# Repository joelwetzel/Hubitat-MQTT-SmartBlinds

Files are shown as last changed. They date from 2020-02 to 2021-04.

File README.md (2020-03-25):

# Hubitat MQTT SmartBlinds
**Hardware, Firmware, and Hubitat Driver for MQTT Smart Blinds**

This is a work in progress.  I don't expect anyone else will ever build one of these, but I wanted to document it, for my own ease of replicating it again.

The hardware and firmware is heavily based on the work of Smart Home Hookup here:  https://github.com/thehookup/Motorized_MQTT_Blinds, and here:  http://www.thesmarthomehookup.com/automated-motorized-window-blinds-horizontal-blinds/  Much thanks to that dude!  Watch his youtube video before following my instructions.

The Hubitat driver is my own creation, using the MQTT support that Hubitat added last year.

What I've tried to do that is beyond what Smart Home Hookup did is two things:
- Make it work well with Hubitat
- "Productize" it.  Hide all the hardware details and make it clean and minimal, repeatable to build, and easy to maintain.

----------

## Parts List
Stepper Motors: https://amzn.to/2D5rVsF

Stepper Drivers: https://amzn.to/2OZqW1W

NodeMCU: https://amzn.to/2I89xDF

Buck Converter: https://amzn.to/2UsQ7jA

12V Power Supply: https://www.amazon.com/gp/product/B07THWH1KZ

DC extension cables and barrel connector:  https://www.amazon.com/gp/product/B01EAHRZEC

Cheap ethernet cable to cut up:  https://www.amazon.com/gp/product/B074NBWQST

Ethernet coupler:  https://www.amazon.com/gp/product/B01CLFCX7E

Velcro strips:  https://www.amazon.com/Command-Picture-Decorate-Damage-Free-PH206-14NA/dp/B073XR4X72

Dupont Crimper toolset:  https://www.amazon.com/gp/product/B07GS1Z3M3

----------

## Preparing the Motor Assembly

#### The motor assembly goes into the blinds header.  It has a 3d printed base, the stepper motor itself, a 3d printed adapter to connect the motor to the rod, the driver board, and an ethernet cable sticking out.

1. Print the 2" blinds base:  https://github.com/thehookup/Motorized_MQTT_Blinds/blob/master/BlindsBase.stl.  It can be 30% infill.  Test-fit the stepper in it.  It should fit snugly.  You won't need screws or glue to hold it in, when in place in the blinds.

2. Open the blue cover on the stepper motor and use a screwdriver to scratch out the middle trace.  Use a multimeter to make sure continuity is broken.

3. Shorten the motor wires.  You can completely remove the middle one that went to the middle trace.  Shorten the others to 2.5 inches.  Attach a 4-pin female Dupont connector as shown.  I found this video very helpful for learning how to use my Dupont crimper:  https://www.youtube.com/watch?v=-u1t7Cdf6RE&t=376s

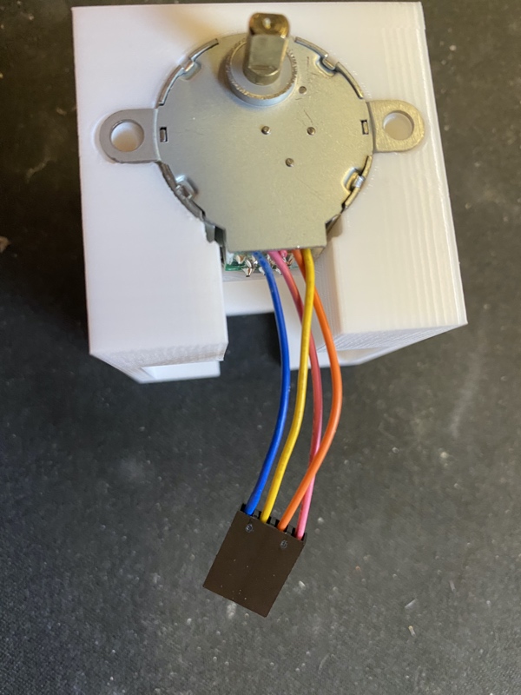
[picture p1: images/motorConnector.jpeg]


4. Prepare the stepper driver board.  You need to create a solder bridge between the reset pin and the sleep pin (the green jumper in this pic), and trim off any unused pins.

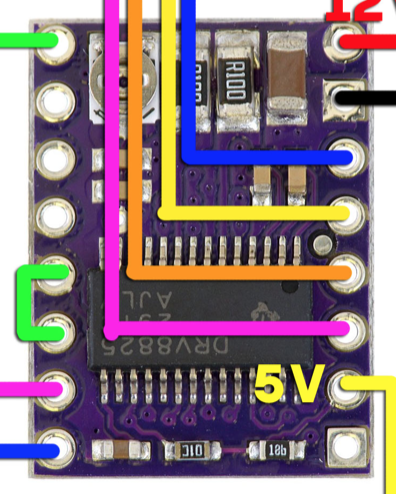
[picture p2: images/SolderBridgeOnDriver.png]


5. Pull down your blinds.
6. Remove any end caps, if it has them.
7. Remove the pull string assembly that turns the rod when you pull the strings.

8. You'll need to print an adapter to connect the stepper shaft to the rod in the blinds.  The rods can have lots of different shapes.  Smart Home Hookup provided several options.  I designed my own, since my rod had a profile like the superman emblem.  I've uploaded that STL here. (Adapter.stl)  Print it at 100% infill.  (By this point, you should have your blinds partially dismantled.  Smart Home Hookup has a good youtube video on doing that.)

9. Prepare the ethernet cable that will come out of the motor assembly.  It should be about 6 inches long.  Attach Dupont connectors as shown here:

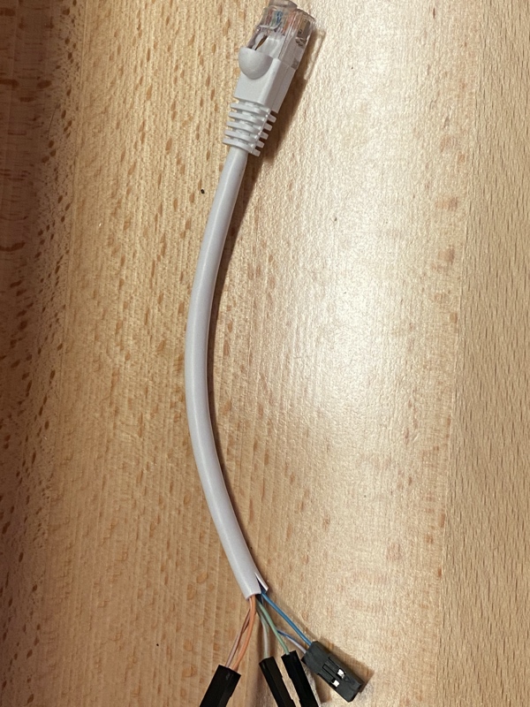
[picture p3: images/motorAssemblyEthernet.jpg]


10. Attach the connectors from both the ethernet cable and the motor onto the driver board, as shown here:

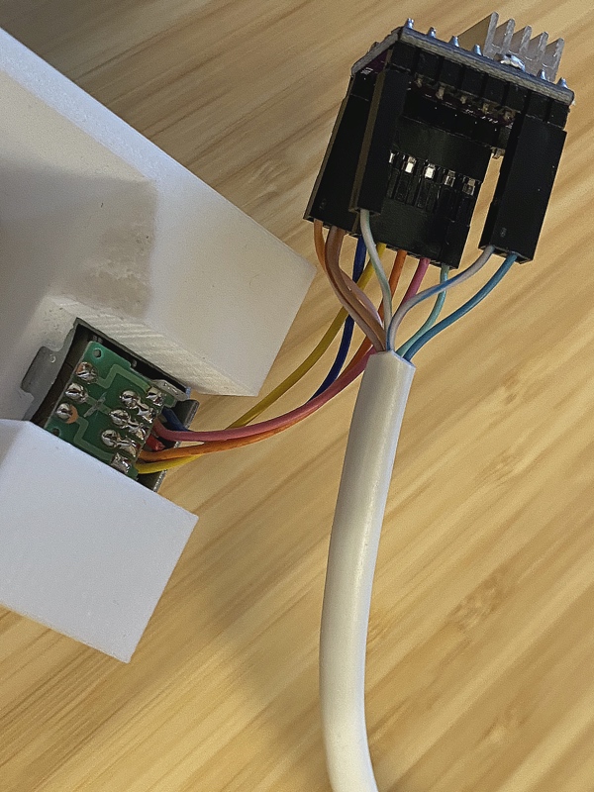
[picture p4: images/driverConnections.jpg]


11. After putting the blinds base, the motor, and the adapter in, I had to shorten my rod.  I let the excess stick out the opposite side, and used a dremel to cut through it.

12. Assemble the Motor Assembly inside the blinds.  The driver gets tucked into the cavity in the blinds base.  You'll need to find a route to get the ethernet cable out of the blinds.  It'll look something like this:

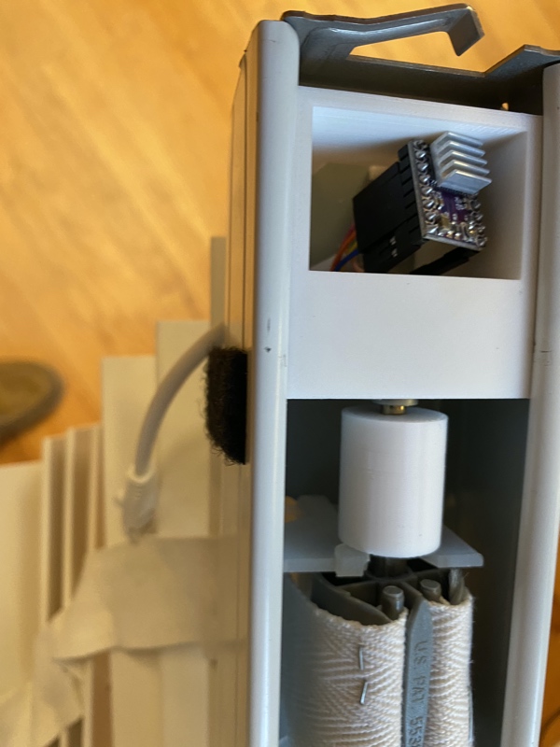
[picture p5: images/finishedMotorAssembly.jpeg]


13. Reinstall the blinds in the window.

----------

## Preparing the Control Unit

#### The Control Unit has a NodeMCU (ESP8266), a buck converter, a two-part 3d printed box, a power cable in, and an ethernet cable out.

1. Solder pins into the buck converter.  Easiest way to do this is to stick it onto a breadboard, so that forces the pins to align well.

2. At this point, you MUST calibrate the buck converter to output 5V.  If you don't, you'll burn up your NodeMCU.  (Yes, technically an ESP8266 chip itself is spec'ed for 3.3V, but this'll work at 5.  I believe it's because the NodeMCU has an extra voltage regulator.)

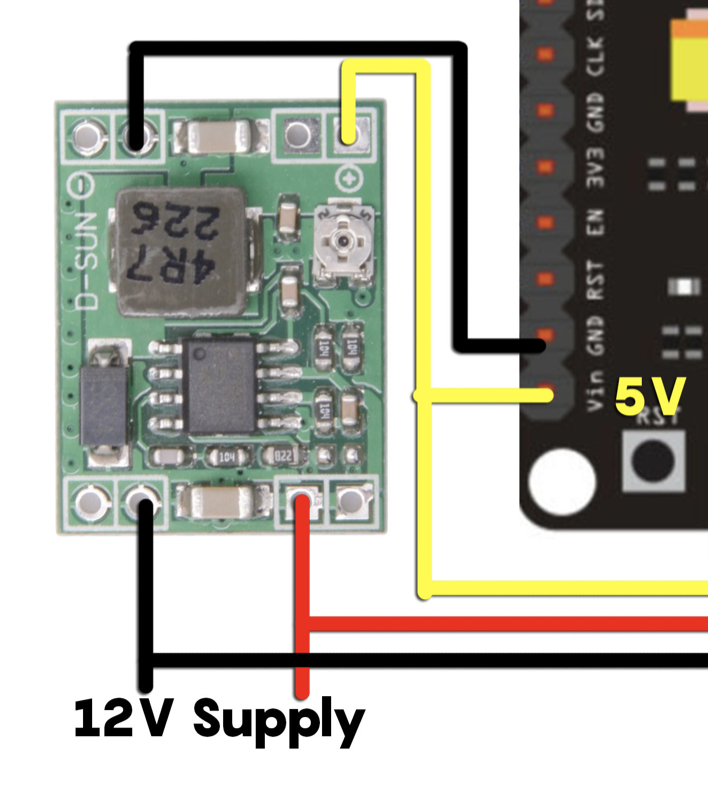
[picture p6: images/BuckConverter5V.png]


3. Assemble the breadboard.  The goals are:  Get 12V in.  Convert it down to 5V.  Get that 5V in to the NodeMCU.  Have the 12V available for the stepper driver.  Make it easy to connect the stepper driver.  Here's what it should look like:

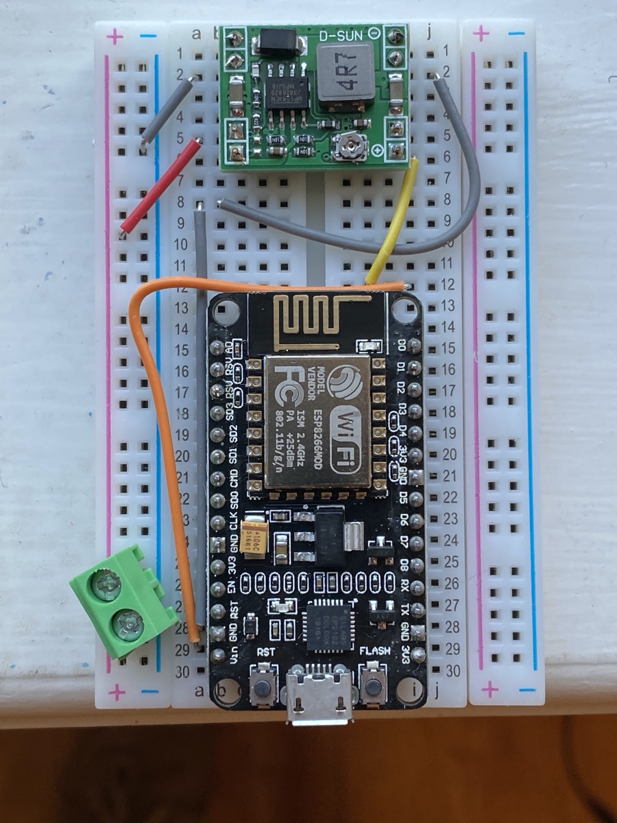
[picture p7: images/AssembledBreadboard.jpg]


4. Clip off any tabs that are sticking out of the breadboard.

5. 3D Print the bottom of the box that the breadboard goes into.  It's ControlUnitBottom.stl.

6. Use a sticky pad to attach the breadboard inside the box.  Make sure the micro USB port lines up with the opening for it, so you can reprogram the NodeMCU.

7. Prepare the ethernet cable to come out of the box, with MALE Dupont connectors.  You'll need to attach the Dupont connectors while it's already sticking through the hole in the box.  Here are the Dupont connectors you'll want. The connections are:

  - Double orange and Double red go to +12V and ground.
  - Green goes to the +5V.
  - Green-strip, blue, and blue-strip go to D5, D6, and D7.

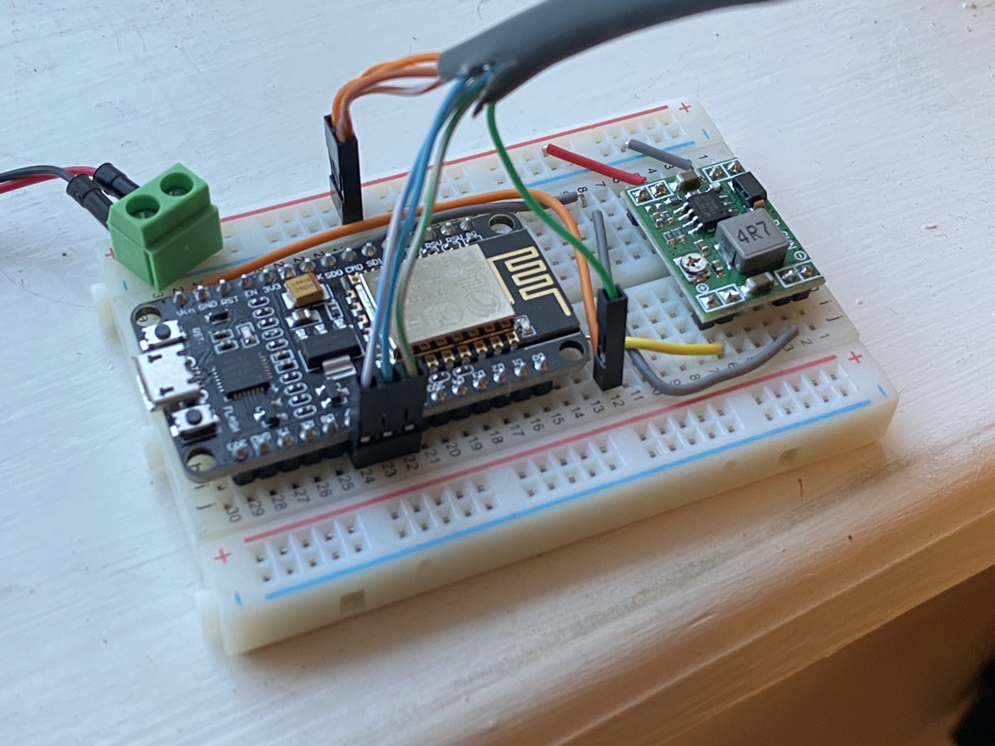
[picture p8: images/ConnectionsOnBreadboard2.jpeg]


8. Attach the female power plug.  At this point, it should look something like this:

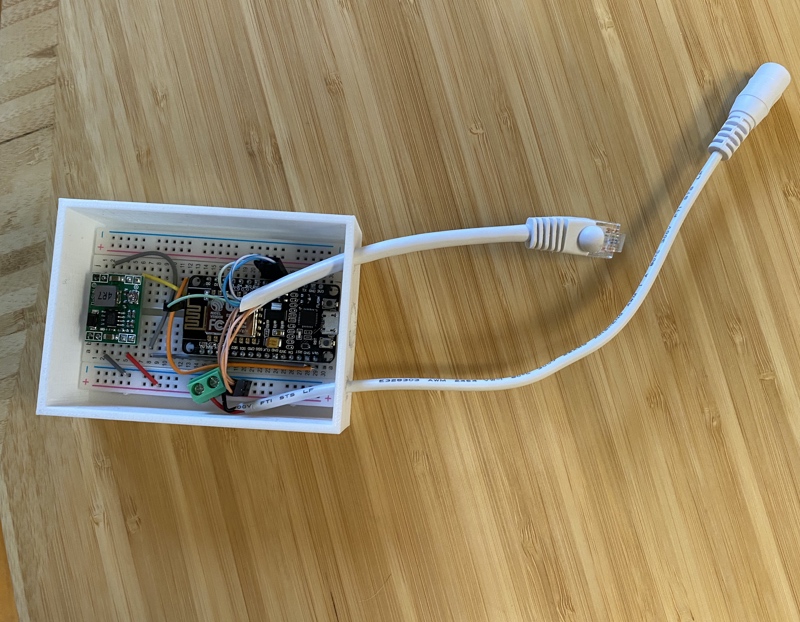
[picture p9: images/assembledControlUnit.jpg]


9. 3D print the top of the box.  It's ControlUnitTop.stl.

10. Assemble.  You should be able to attach a micro USB cable for programming at this point.

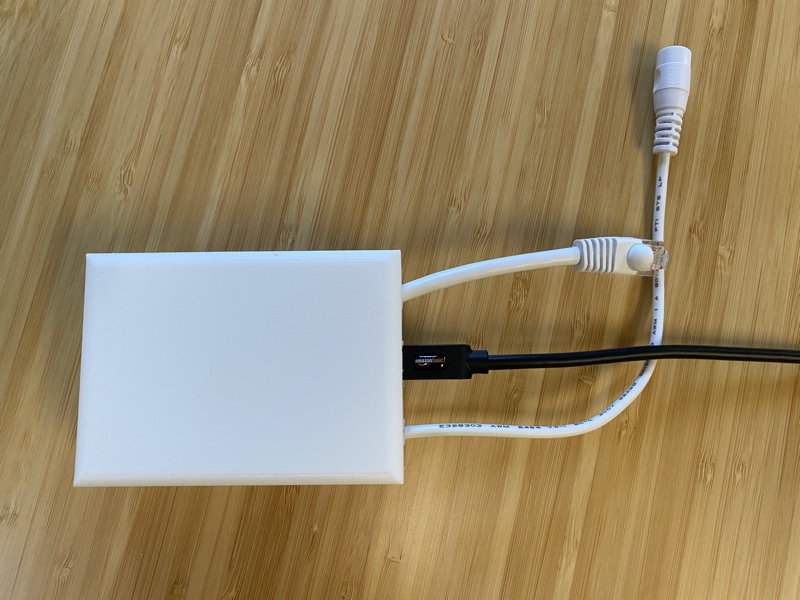
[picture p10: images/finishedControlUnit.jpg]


----------

## Final Assembly
Connect the ethernet from the Motor Assembly to the ethernet from the Control Unit using the ethernet female-to-female coupler.  Tuck the control unit up behind the blinds and run power.  It should be almost invisible.  Just a small power cord visible in the lower left of the window opening.

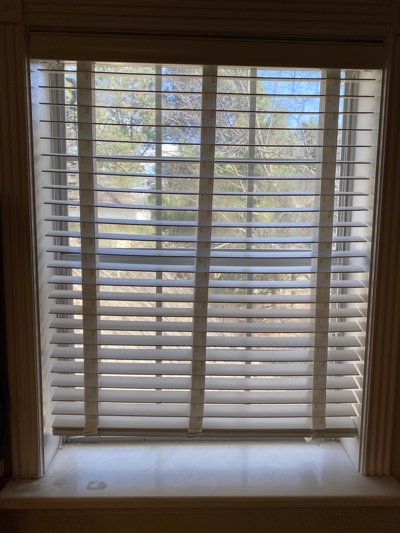
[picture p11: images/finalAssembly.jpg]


----------

## Setting up an MQTT Broker
I'll let others explain this.  There are lots of good tutorials out there.  I use Mosquitto.

----------

## Installing the Firmware
You'll need to install the firmware on the NodeMCU in the Control Unit.  That's why it has the Micro USB port.  I've provided the main.cpp file with the firmware.  I use Platform.io, though I haven't uploaded the entire project.  You can also just use the Arduino IDE.
- You'll need to set your WIFI and MQTT info in main.cpp.
- You need to set USER_DEVICE_NETWORK_ID for the id you're going to assign the device in Hubitat.

----------

## Installing the Hubitat Driver
I've provided the driver that will control the Device in Hubitat.  You need to make sure your Device Network ID in Hubitat matches what you set in the firmware.

----------

## Controlling with Siri/HomeKit
This driver/device works great with the Hubitat plugin for Homebridge.  Using that, you can control the blinds very well from within the Home app on your iPhone, or with Siri.

----------

## Controlling with Alexa
The Hubitat Alexa skill does not yet support window shades and blinds.  To enable Alexa to work with my blinds, I created my own Alexa skill here:  https://github.com/joelwetzel/Alexa-Skill-For-Hubitat-Shades-And-Blinds

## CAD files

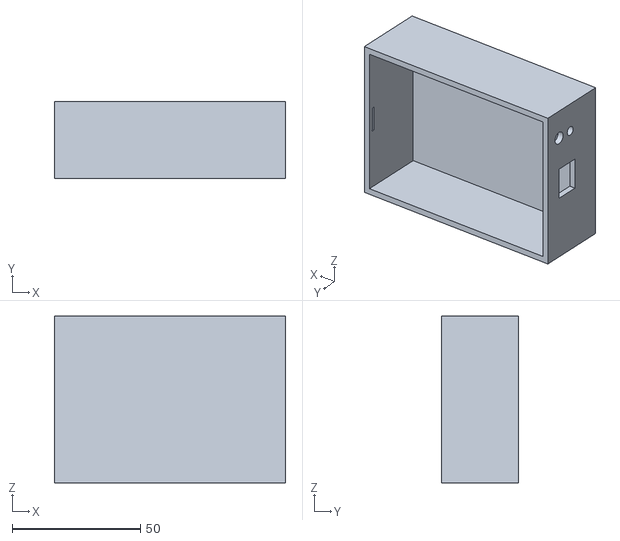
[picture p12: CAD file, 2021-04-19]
3dPrintedComponents/ControlUnitBottom.stl
90.0 x 30.0 x 65.0

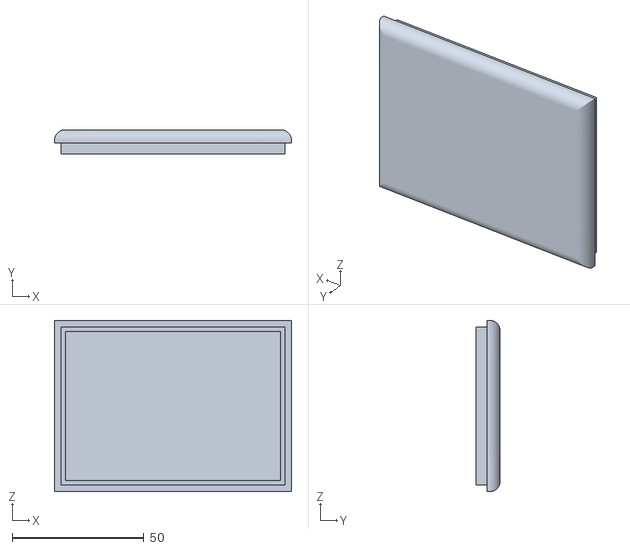
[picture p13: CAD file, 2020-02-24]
3dPrintedComponents/ControlUnitTop.stl
90.0 x 9.25 x 65.0

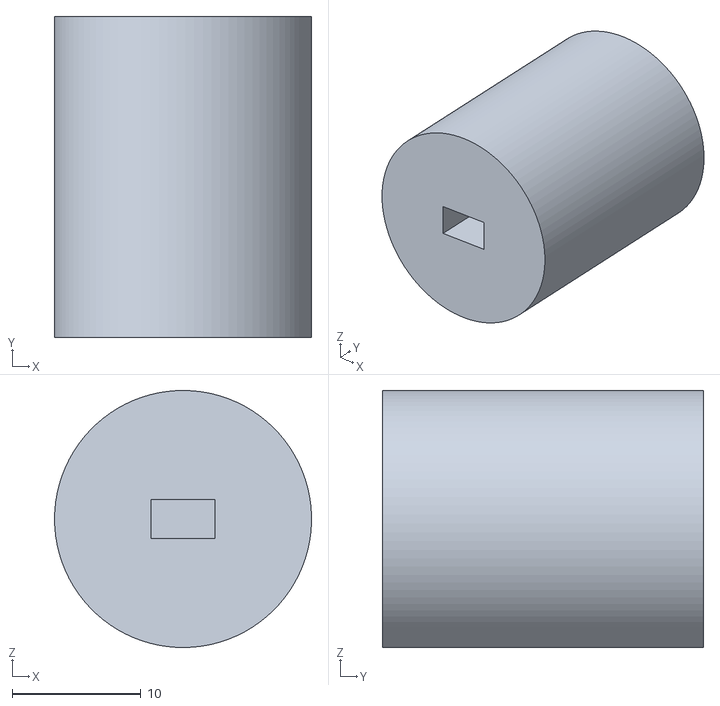
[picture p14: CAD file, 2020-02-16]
3dPrintedComponents/Adapter.stl
20.0 x 25.0 x 20.0

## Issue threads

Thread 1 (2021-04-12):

ControlUnitBottom.stl Missing

hexonMD, 2021-04-12:
Any chance you could add this STL?

joelwetzel, 2021-04-19:
Added the missing file.

Closed 2021-04-19.

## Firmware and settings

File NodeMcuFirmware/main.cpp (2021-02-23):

#include <SimpleTimer.h>    // https://github.com/marcelloromani/Arduino-SimpleTimer/tree/master/SimpleTimer
#include <ESP8266WiFi.h>    // if you get an error here you need to install the ESP8266 board manager 
#include <ESP8266mDNS.h>    // if you get an error here you need to install the ESP8266 board manager 
#include <PubSubClient.h>   // https://github.com/knolleary/pubsubclient
#include <ArduinoOTA.h>     // https://github.com/esp8266/Arduino/tree/master/libraries/ArduinoOTA
#include <AH_EasyDriver.h>  // http://www.alhin.de/arduino/downloads/AH_EasyDriver_20120512.zip


/*****************  START USER CONFIG SECTION *********************************/

#define WIFI_SSID                 "*****"
#define WIFI_PASSWORD             "*****"
#define USER_MQTT_SERVER          "mqtt.local"
#define USER_MQTT_PORT            1883

// Uncomment if your MQTT broker requires authentication
//#define USER_MQTT_USERNAME        "YOUR_MQTT_USER_NAME"
//#define USER_MQTT_PASSWORD        "YOUR_MQTT_PASSWORD"

#define USER_DEVICE_NETWORK_ID     "officeBlindsRight"         // This must match the Device Network ID in Hubitat

#define STEPPER_SPEED             17                  // Defines the speed in RPM for your stepper motor
#define STEPPER_STEPS_PER_REV     1028                // Defines the number of pulses that is required for the stepper to rotate 360 degrees
#define STEPPER_MICROSTEPPING     0                   // Defines microstepping 0 = no microstepping, 1 = 1/2 stepping, 2 = 1/4 stepping 
#define DRIVER_INVERTED_SLEEP     1                   // Defines sleep while pin high.  If your motor will not rotate freely when on boot, comment this line out.

#define STEPS_TO_CLOSE            8                   // Defines the number of steps needed to open or close fully
#define CLOSE_DIRECTION           0                   // Switch between 1 and 0 to make the blinds close the opposite direction (1 if motor is on right of blinds rod.  0 if motor is on left.)

#define STEPPER_DIR_PIN           D6
#define STEPPER_STEP_PIN          D7
#define STEPPER_SLEEP_PIN         D5
#define STEPPER_MICROSTEP_1_PIN   14
#define STEPPER_MICROSTEP_2_PIN   12

#define LIGHT_SENSOR_PIN          A0
#define LIGHT_RANGE_MIN           0
#define LIGHT_RANGE_MAX           1000

/*****************  END USER CONFIG SECTION *********************************/


WiFiClient espClient;
PubSubClient client(espClient);
SimpleTimer timer;
AH_EasyDriver shadeStepper(STEPPER_STEPS_PER_REV, STEPPER_DIR_PIN ,STEPPER_STEP_PIN,STEPPER_MICROSTEP_1_PIN,STEPPER_MICROSTEP_2_PIN,STEPPER_SLEEP_PIN);

// Global Variables
bool boot = true;
int currentPosition = 0;
int newPosition = 0;
char positionPublish[50];
char lightIntensityPublish[50];
bool moving = false;

const char* ssid = WIFI_SSID ; 
const char* password = WIFI_PASSWORD ;
const char* mqtt_server = USER_MQTT_SERVER ;
const int mqtt_port = USER_MQTT_PORT ;

// Uncomment if your MQTT broker requires authentication
//const char *mqtt_user = USER_MQTT_USERNAME ;
//const char *mqtt_pass = USER_MQTT_PASSWORD ;

const char *mqtt_device_network_id = USER_DEVICE_NETWORK_ID ; 


//Functions
void setup_wifi()
{
  // We start by connecting to a WiFi network
  Serial.println();
  Serial.print("Connecting to ");
  Serial.println(ssid);

  WiFi.begin(ssid, password);

  while (WiFi.status() != WL_CONNECTED) {
    delay(500);
    Serial.print(".");
  }

  delay(500);

  Serial.println("");
  Serial.println("WiFi connected");
  Serial.println("IP address: ");
  Serial.println(WiFi.localIP());
}


void flashLed(int numFlashes, long d)
{
  for (int i = 0; i < numFlashes; i++)
  {
    digitalWrite(LED_BUILTIN, LOW);
    delay(d);
    digitalWrite(LED_BUILTIN, HIGH);
    delay(d);
  }
}


void reconnect()
{
  int retries = 0;
  int maxRetries = 150;

  while (!client.connected())
  {
    if(retries < maxRetries)
    {
      Serial.print("Attempting MQTT connection...");
      if (client.connect(mqtt_device_network_id))   // Password option:  client.connect(mqtt_device_network_id, mqtt_user, mqtt_pass)
      {
        Serial.println("connected");

        flashLed(3, 500);

        if(boot == false)
        {
          client.publish("hubitat/"USER_DEVICE_NETWORK_ID"/status/device", "Reconnected"); 
        }
        if(boot == true)
        {
          client.publish("hubitat/"USER_DEVICE_NETWORK_ID"/status/device", "Rebooted");
          client.publish("hubitat/"USER_DEVICE_NETWORK_ID"/windowShade/attributes/position", "0"); 
          boot = false;
        }
        // ... and resubscribe
        client.subscribe("hubitat/"USER_DEVICE_NETWORK_ID"/windowShade/commands/setPosition");
      } 
      else 
      {
        flashLed(10, 100);

        Serial.print("failed, rc=");
        Serial.print(client.state());
        Serial.println(" try again in 5 seconds");
        retries++;
        // Wait 5 seconds before retrying
        delay(5000);
      }
    }

    if(retries >= maxRetries)
    {
      ESP.restart();    // TODO - this could be a problem.  If it restarts in closed position...  Maybe if we hit this, I should treat it like a setPosition(open), but set a flag to restart when we get there.
    }
  }
}


void mqttCallback(char* topic, byte* payload, unsigned int length) 
{
  Serial.print("Message arrived [");

  Serial.print(topic);
  Serial.print("] ");
  
  if (strcmp(topic, "hubitat/"USER_DEVICE_NETWORK_ID"/windowShade/commands/setPosition") == 0)
  {
    payload[length] = '\0';

    int intPayload = atoi((char *) payload);

    Serial.println(intPayload);
    Serial.println();
    
    newPosition = intPayload;

    flashLed(4, 20);
  }
}


void processStepper()
{
  digitalWrite(16, LOW);
  delay(10);
  digitalWrite(16, HIGH);

  if (newPosition > currentPosition)
  {
    #if DRIVER_INVERTED_SLEEP == 1
    shadeStepper.sleepON();
    #endif
    #if DRIVER_INVERTED_SLEEP == 0
    shadeStepper.sleepOFF();
    #endif

    #if CLOSE_DIRECTION == 1
    shadeStepper.move(80, FORWARD);
    #endif
    #if CLOSE_DIRECTION == 0
    shadeStepper.move(80, BACKWARD);
    #endif

    currentPosition++;
    moving = true;
  }

  if (newPosition < currentPosition)
  {
    #if DRIVER_INVERTED_SLEEP == 1
    shadeStepper.sleepON();
    #endif
    #if DRIVER_INVERTED_SLEEP == 0
    shadeStepper.sleepOFF();
    #endif

    #if CLOSE_DIRECTION == 1
    shadeStepper.move(80, BACKWARD);
    #endif
    #if CLOSE_DIRECTION == 0
    shadeStepper.move(80, FORWARD);
    #endif

    currentPosition--;
    moving = true;
  }

  if (newPosition == currentPosition && moving == true)
  {
    #if DRIVER_INVERTED_SLEEP == 1
    shadeStepper.sleepOFF();
    #endif
    #if DRIVER_INVERTED_SLEEP == 0
    shadeStepper.sleepON();
    #endif

    itoa(currentPosition, positionPublish, 10);
    client.publish("hubitat/"USER_DEVICE_NETWORK_ID"/windowShade/attributes/position", positionPublish); 
    moving = false;
  }
  
  //Serial.println(currentPosition);
  //Serial.println(newPosition);
}


void checkIn()
{
  client.publish("hubitat/"USER_DEVICE_NETWORK_ID"/status/device", "OK"); 
}


void measureLightSensor()
{
  int sensorValue = analogRead(LIGHT_SENSOR_PIN);

  //Serial.println(sensorValue); 

  int scaledValue = map(sensorValue, 0, 1024, LIGHT_RANGE_MIN, LIGHT_RANGE_MAX); // + LIGHT_RANGE_MAX / 2);

  //scaledValue = scaledValue - LIGHT_RANGE_MAX/2;

//Serial.print("Scaled: ");
//Serial.println(scaledValue);

  if (scaledValue < 0)
  { scaledValue = 0; }
  if (scaledValue > LIGHT_RANGE_MAX)
  { scaledValue = LIGHT_RANGE_MAX; }

//Serial.print("Clamped: ");
//Serial.println(scaledValue);

  itoa(scaledValue, lightIntensityPublish, 10);
  client.publish("hubitat/"USER_DEVICE_NETWORK_ID"/illuminanceMeasurement/attributes/illuminance", lightIntensityPublish); 
}


void setup() {
  Serial.begin(9600);

  pinMode(LED_BUILTIN, OUTPUT); 
  pinMode(16, OUTPUT);
  
  shadeStepper.setMicrostepping(STEPPER_MICROSTEPPING);            // 0 -> Full Step                                
  shadeStepper.setSpeedRPM(STEPPER_SPEED);     // set speed in RPM, rotations per minute

  #if DRIVER_INVERTED_SLEEP == 1
  shadeStepper.sleepOFF();
  #endif
  #if DRIVER_INVERTED_SLEEP == 0
  shadeStepper.sleepON();
  #endif
  
  WiFi.mode(WIFI_STA);
  setup_wifi();
  
  client.setServer(mqtt_server, mqtt_port);
  client.setCallback(mqttCallback);
  ArduinoOTA.setHostname(USER_DEVICE_NETWORK_ID);
  ArduinoOTA.begin();

  delay(10);
  
  timer.setInterval(((1 << STEPPER_MICROSTEPPING)*5800)/STEPPER_SPEED/2, processStepper);   
  timer.setInterval(90000, checkIn);
  timer.setInterval(60 * 1000, measureLightSensor);
}


void loop() 
{
  if (!client.connected()) 
  {
    reconnect();
  }

  client.loop();
  ArduinoOTA.handle();
  timer.run();
}

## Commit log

2020-02-08 Update the driver to actually talk to a real ESP8266 device.
2020-02-28 Moved stl files
    [Adapter.stl, ControlUnitTop.stl]
2020-02-28 Moving driver/firmware
2021-02-23 Fixed up string handling to prevent crashes. Flashing LEDs to indicate connection state.
    [main.cpp]
